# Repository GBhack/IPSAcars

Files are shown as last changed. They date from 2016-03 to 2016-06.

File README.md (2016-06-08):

# IPSAcars : Evolution de véhicules autonomes dans un environnement urbain intelligent

## Description du projet :
Réalisation une maquette simulant un environement urbain comprenant des feux de signalisation "intelligents" (c´est à dire s´adaptant à la circulation) à l´ aide d´ une carte FPGA et, dans le même temps, des véhicules autonomes (à l´ aide d'un BeagleBone) capables de circuler dans cet environnement.

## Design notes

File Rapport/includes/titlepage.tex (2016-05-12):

\begin{titlepage}
\newgeometry{top=2cm,bottom=2cm}

\newcommand{\HRule}{\rule{\linewidth}{0.5mm}} % Defines a new command for the horizontal lines, change thickness here

\center % Center everything on the page
 
%----------------------------------------------------------------------------------------
%   HEADING SECTIONS
%----------------------------------------------------------------------------------------

\\[1.5cm]

\textsc{\Large Projet Electif}\\[0.5cm] % Major heading such as course name
\textsc{\large Projet technique}\\[0.5cm] % Minor heading such as course title

{\normalsize \today}\\[1.5cm]

%----------------------------------------------------------------------------------------
%   TITLE SECTION
%----------------------------------------------------------------------------------------

\HRule \\[0.4cm]
{ \Large \bfseries Evolution de véhicules autonomes dans un environnement urbain intelligent}\\[0.4cm] % Title of your document
\HRule \\[2.5cm]

%----------------------------------------------------------------------------------------
%   LOGO SECTION
%----------------------------------------------------------------------------------------

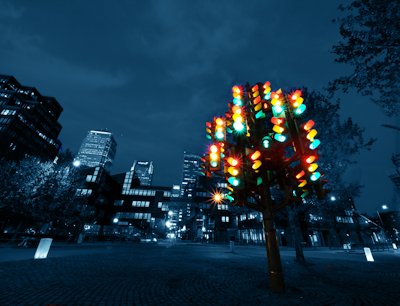
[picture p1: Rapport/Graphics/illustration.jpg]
 \\[2.5cm]

%----------------------------------------------------------------------------------------
%   AUTHOR SECTION
%----------------------------------------------------------------------------------------
{\normalsize Auteurs:}\\
\small
\textsc{Biton} Guillaume (guillaume.biton@ipsa.fr)\\
\textsc{Guichard} Marc-Antoine \small(marc-antoine.guichard@ipsa.fr)\\
\textsc{Lhermite} Camille \small(camille.lhermite@ipsa.fr)\\
\textsc{Monnot} Maxime \small(maxime.monnot@ipsa.fr)\\[1cm]

%----------------------------------------------------------------------------------------

\vfill % Fill the rest of the page with whitespace

\restoregeometry

\end{titlepage}

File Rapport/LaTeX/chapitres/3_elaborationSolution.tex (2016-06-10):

\subsection{Circuit}

	\subsubsection{Structure}

		Le circuit sera principalement composé de medium de 5mm d'épaisseur (matériau résistant, léger, peu fragile, facilement usinable et peu cher) reposant sur une structure une taseaux (de manière à surelever le plateau, afin de passer les câbles en dessous et laisser de la place pour les systèmes de fixation, par exemple ainsi que pour rigidifier la structure (le medium étant un matériau souple)).\\

		Nous avons décidé de donner à la "piste" du circuit la forme suivante :

		\illu{formePiste.pdf}{Forme de la "piste"  du circuit}{0.6}

		Ainsi, nous avons un carrefour à feux ainsi que quatre intersections, soit un large éventail de possibilités.\\

		Après avoir fait une rapide estimation des dimensions de notre robot, nous avons déduit que le circuit devrait faire environ deux mètres par deux mètres.
		Nous avons préféré ajouter vingt centimètres de côté par sécurité.\\

		Ces dimensions étant importantes, ceci nous a conforté dans l'idée que notre circuit devrait être fait en deux parties afin d'en faciliter le rangement. Nous fabriquerions donc deux cadres de deux mètres vingt par un mètre dix qui pourront être facilement assemblés.

	\subsubsection{Feux}

		Les feux seront comprendront chacun deux LED "haute luminosité" de 5mm : une rouge et une verte. Trois fils seront donc nécéssaires pour chaque feu : deux pour les alimentations de chacune des LEDs et une masse commune. Avec les quatre feux, le circuit comptera donc huit LEDs et douze fils différents.\\
		\newpage
		Les feux seront dans la mesure du possible imprimés en 3D :\\
		\begin{figure}[ht!]
			\centering
			\begin{minipage}{0.4\textwidth}
				\raggedleft
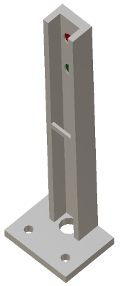
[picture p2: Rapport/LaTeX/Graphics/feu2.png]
				
			\end{minipage}\hfill
			\begin{minipage}{0.4\textwidth}
				\raggedright
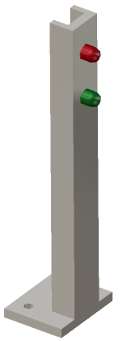
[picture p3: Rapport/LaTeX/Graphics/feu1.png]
				
			\end{minipage}
			\caption{Maquette numérique d'un feu bicolore}
		\end{figure}

		\vspace{15pt}

		Notons la présence de deux petits trous pour enficher les feux sur des vis et d'un plus gros pour le passage des fils. Un passe-câble est également intégré à la "goulotte" qui constitue le montant du feu afin de guider les fils.

	\subsubsection{Capteurs}

		Afin d'adapter le comportement des feux à l'état du trafic, encore faut-il que la carte FPGA dispose d'un moyen d'évaluer ce trafic.\\

		Nous disposerons donc sur la piste des capteurs "ILS" (Interrupteur à Lame Souple) \nomenclature{ILS}{Interrupteur à Lame Souple} sur la piste aux abords des feux. Les ILS sont de petits composants se comportant comme un interrupteur ouvert en temps normal, et comme un interrupteur fermé lorsqu'on approche un aimant.\\

		En munissant nos robots d'un aimant bien placé, ces derniers fermeront temporairement le circuit lors de leur arrivée aux abords des feux.\\

		Cette solution est extremement simple et ne nécéssite aucun traitement du signal (contrairement aux capteurs à effet hall ou fourches optiques, souvent utilisés en détection de présence).

\newpage
\subsection{Robot}

	\subsubsection{Suivi de trajectoire}

		Afin d’offrir une capacité de suivi de trajectoire simple et robuste, il a été décidé d’intégrer au robot la fonctionnalité "suivi de ligne". Il s’agit de l’une des méthodes les plus répandues\cite{bib3} \cite{bib4}, relativement simple à implémenter et économe aussi bien en composants qu’en puissance de calcul nécessaire.\\

		L’idée est d’offrir une base fiable et simple pour que le suivi de trajectoire ne soit pas une source de préoccupation ou d’erreur dans le cas d'utilisations centrées sur d’autres problématiques (dans le cadre d'un TP sur la reconnaissance d'image, par exemple). Cela n’exclut cependant pas qu’un étudiant ou chercheur désireux d’explorer d’autres possibilités de suivi de trajectoire (via la caméra, un dispositif de triangulation ou autre) puisse se passer de ce module et exploiter une autre solution.\\

		Le principe de suivi de ligne est relativement simple : on place sur l’axe du robot, quelques millimètres au-dessus du sol, un capteur appelé « réflecteur optique ». Ce capteur émet une onde lumineuse (souvent infrarouge) et une cellule mesure l’intensité reçue sur la longueur d’onde émise. Une forte intensité reçue indiquera la présence d’une surface réfléchissante, tandis qu’une faible intensité indiquera la présence d’une surface absorbante. Il est ainsi aisé de différencier un fond sombre (la « route ») d’une ligne blanche.\\

		Une loi linéaire lie la tension lue en sortie de capteur à l'intensité reçue.\\
		Une simple lecture de cette tension permet, après comparaison avec des valeurs "seuil" définies expérimentalement, de savoir si le capteur se trouve au dessus d'une ligne blanche ou non.\\

		Sur les schémas suivants, pour des raisons d'imprimabilité et de lisibilité, les lignes seront noires et le revêtement du circuit sera blanc.\\

		\begin{figure}[H]
			\centering
			\begin{minipage}{0.48\textwidth}
				\centering
				
				\caption{Capteur au dessus d'un support sombre}
			\end{minipage}\hfill
			\begin{minipage}{0.48\textwidth}
				\centering
				
				\caption{Capteur au dessus d'un support clair}
			\end{minipage}
		\end{figure}

		La question qui se pose est celle du nombre de capteurs, et de leur disposition.\\

		Il est tout à fait possible de n'utiliser qu'un capteur : chaque fois qu'il quitte la ligne blanche, on entamera un virage à droite (puis à gauche si on ne retrouve pas la ligne blanche dans les quelques millisecondes suivantes) jusqu'à retrouver la ligne. Il est évident que cette méthode ne permettra pas une très grande fluidité de déplacement pour notre robot.

		\illu{capteurSimpleGauche.pdf}{Dépassement de la ligne sur la gauche}{1}
		\illu{capteurSimpleDroite.pdf}{Dépassement de la ligne sur la droite}{1}

		L'utilisation de deux capteurs permet une meilleure fluidité. On placera cette fois un capteur de chaque côté de la ligne.

		\illu{capteurDoubleGauche.pdf}{Dépassement de la ligne sur la gauche}{1.4}
		\illu{capteurDoubleDroit.pdf}{Dépassement de la ligne sur la droite}{1.4}

		Notons que, quelque soit la méthode employée, le suivi de ligne se résume toujours à un "rebondissement" des capteurs sur la ligne. Aussi, pour obtenir une trajectoire aussi rectiligne que possible, il faudra "resserer" les capteurs au maximum autour de la ligne, et appliquer des corrections de faible amplitude.

		\illu{capteurDoubleEcartFort.pdf}{Ecart important entre les capteurs}{1}
		\illu{capteurDoubleEcartFaible.pdf}{Ecart réduit entre les capteurs}{1}

		Nous pourrons éventuellement introduire un amortissement progressif de la correction via un régulateur PID\nomenclature{PID}{Proportionnel, Intégrateur, Dérivateur}, mais cela peut introduire de nombreuses problématiques dans des cas d'utilisation plus complexes.\\

		Nous retiendrons donc à ce stade la solution consistant en deux capteurs placés de part et d'autre de la ligne. Nous veillerons à ce que le placement des capteurs permette une détection de très faibles écarts de trajectoire, sans pour autant induire des ambiguïtés de mesure.\\

		Intéressons nous maintenant au cas d'une trajectoire courbe. Le fait d'avoir privilégié l'application de faibles corrections peut alors s'avérer problématique si ces dernières ne sont pas suffisantes pour adapter la trajectoire.

		\illu{perteTrajectoireVirage.pdf}{Perte de trajectoire en virage dû à de trop faibles corrections}{1.5}

		Pour obtenir un fluidité de déplacement raisonnable tout en assurant la possibilité de suivre des trajectoires courbes à rayon de virage réaliste, nous placerons une deuxième série de capteurs "encadrant" les capteurs principaux. Une détection de ligne par ces capteurs déclanchera une correction plus importante.

		\illu{trajectoireVirage.pdf}{Maîtrise de la trajectoire en virage grâce à l'utilisation de 4 capteurs}{1.5}

		Cette solution consistant en l'utilisation de quatre réflecteurs optiques alignés de manière à encadrer de près la ligne à suivre est sans doute l'une des plus simples imaginables en terme de réalisation mais également d'utilisation et de maintenance.
		Elle n'est malheureusement pas suffisante pour répondre à notre besoin. En effet, cette solution trouvera ses limites dès lors que notre Robot rencontrera sa première intersection, élément capital de ce projet.\\

		\illu{intersection4Capteurs.pdf}{Robot incapable de répondre à la présence d'une intersection}{1.5}

		Si on trouve dans la littérature de très nombreux exemples de réalisations de robots suiveurs de lignes, ces dernières se limitent toujours à des circuits sous forme de boucle. Notre défi est donc de mettre au point une solution permettant l'évolution du robot sur un circuit comprenant des intersections. Notre robot devra ne pas être "perturbé" au passage d'une intersection, mais surtout être capable d'emprunter toutes les directions qui lui sont offertes.\\

		La solution que nous avons mis au point consiste en l'introduction d'un capteur central et l'adoption d'un comportement "mono-latéralement centré" du robot lors de la traversée d'intersections : lorsqu'il arrivera sur une intersection, le robot ne se souciera plus que de garder son capteur central sur la ligne, et ses capteurs latéraux \textbf{du côté de la direction choisie} à l'écart de cette dernière.

		\illu{intersection5CapteursTD.pdf}{Suivi de trajectoire sur une intersection (en choisissant d'aller tout droit)}{1.5}
		\illu{intersection5CapteursDroite.pdf}{Suivi de trajectoire sur une intersection (en choisissant d'aller à droite)}{1.5}

		Notons que la forme de la ligne devra être intelligemment faite, en présentant des rayons de courbure réalistes (un véhicule ne peut pas tourner à angle droit) et des intersections réalisables (notamment via l'utilisation de deux lignes séparées pour la circulation en sens contraires).\\

		Voici donc à quoi ressemblerait un carrefour:
		\illu{carrefour.pdf}{Carrefour en représentation "lignes"}{1.4}

		Pour pleinement définir la logique mise au point, illustrons la au travers de la situation la plus complexe que pourra rencontrer notre robot, qui est celle de la bifurcation à gauche.

		\illu{carrefour5capteursGauche.pdf}{Cas du virage à gauche sur un carrefour avec cinq capteurs}{1.5}

		\begin{enumerate}
			\item Le premier croisement ne nous intéresse pas. Nous allons continuer tout droit et éteignons donc la moitié droite de nos capteurs.
			\item Au passage du croisement, nous éteignons temporairement l'ensemble de nos capteurs.
			\item Le croisement passé, nous éteignons cette fois la moitié gauche de nos capteurs pour ne pas être perturbés par "la voie d'insertion".
			\item Peu de temps après, nous rallumons la moitié gauche et éteignons la moitié droite des capteurs pour suivre la voie bifurquant à gauche.
		\end{enumerate}

		Cette solution semble robuste tout en conservant une certaine simplicité d’implémentation. Elle sous-entend en revanche que le robot "sache" quand il arrive sur une intersection, mais également qu'il puisse évaluer à quelques millimètres près la distance qui le sépare des différentes "parties" de cette intersection (pour activer et désactiver ses capteurs en conséquence).\\

		La solution à cette problématique nous a été inspirée par le souvenir d'un brevet déposé en 2003 par le groupe PSA \cite{bib5}, qui proposait l'utilisation de code-barres tracés sur la route et que des capteurs placés sous le pare-choc des voitures pourraient "lire" pour prévenir le conducteur des sources de danger à venir (intersections, feux...).
		Il fut donc décidé que deux capteurs supplémentaires seraient ajoutés sur les extérieurs. Ils augmenteraient ainsi la précision de placement sur la ligne, mais permettraient surtout de lire des "codes-barres" placés sur la piste. Ces code-barres devraient permettre au robot d'être averti de l'approche d'un carrefour (trois choix de direction possibles) ou d'une simple intersection (deux choix possibles). Nous avons simplement basé notre code sur une ligne simple ou doublée :\\
		\begin{figure}[H]
			\begin{tabu}to \textwidth {@{} | l | *3{X[c]|}@{}}
			  \hline
			   & \textbf{Gauche} & \textbf{Droite} & \textbf{Gauche ET Droite} \\
			  \hline
			  \textbf{Simple} & Impossible de tourner à droite & Impossible de tourner à gauche & Toutes possibilités offertes\\
			  \hline
			  \textbf{Double} & Obligation de tourner à gauche & Obligation de tourner à droite & Impossible d'aller tout droit \\
			  \hline
			\end{tabu}
			\caption{Formalisme employé pour les code-barres}
		\end{figure}

		Un code "doublé" serait composé de deux lignes elles mêmes séparées d'une épaisseur de ligne.
		Les codes seraient placés à 30cm du premier croisement.\\

		Dès la lecture d'un code au sol, le robot sera donc "attentif" à l'éventuelle apparition d'un doublon pendant environ deux centimètres. Si rien n'est lu passé cette distance, il en déduira qu'il s'agit d'un code simple. Il prendra alors une décision de direction (et pourra au passage en avertir les autres robots) et commencera un décompte de distance afin de gérer les activations et désactivations de ses capteurs jusqu'au franchissement de l'intersection.\\

		Illustrons ce système avec le cas de la bifurcation à gauche :

		\illu{carrefour7capteursGauche.pdf}{Cas du virage à gauche sur un carrefour avec sept capteurs}{1.5}

		\begin{enumerate}
			\item Lecture d'un code-barre : dans 30cm le robot aura la possibilité de tourner à droite et à gauche.
			\item Aucun doublon détecté dans les quelques centimètres suivants. La possibilité d'aller tout droit nous est donc offerte. Prise de décision quant à la direction (nous choisissons d'aller à gauche) et avertissement des autres robots en conséquence.
			\item Le premier croisement ne nous intéresse pas. Nous allons continuer tout droit et éteignons donc la moitié droite de nos capteurs.
			\item Au passage du croisement, nous éteignons temporairement l'ensemble de nos capteurs.
			\item Le croisement passé, nous éteignons cette fois la moitié gauche de nos capteurs pour ne pas être perturbés par "la voie d'insertion".
			\item Peu de temps après, nous rallumons la moitié gauche et éteignons la moitié droite des capteurs pour suivre la voie bifurquant à gauche.
		\end{enumerate}

		Le robot doit donc être conscient des distances parcourues avec une précision supérieure à deux centimètres. Le moyen le plus simple d'implémenter cette fonctionnalité est sans aucun doute au travers d'un encodeur incrémental placé sur l'axe de propulsion du robot.\\

		Nous pouvons donc considérer qu'à ce stade, nous disposons d'un solution satisfaisante répondant à la problématique du suivi de trajectoire.
		Cette solution répond précisément aux contraintes du projet, tout en conservant un certain niveau de simplicité. Elle est, pour rappel, constituée des éléments suivants :\\

		\begin{itemize}
			\item \textbf{Sur le circuit :} Un réseau de lignes blanches sur fond noir représentant les trajectoires empruntables par le robot.
			\item \textbf{Sur le robot :} Un ensemble de 7 réflecteurs optiques.
		\end{itemize}

	\subsubsection{Détection d'obstacles et de de signalisation}

		Etant donné le fait que les robots évoluerons dans un environnement idéal, parfait, il n'existera pas en première instance d'obstacles à proprement parler, tel qu'une route barrée aléatoirement, par exemple. Le seul obstacle que nous risquerions de rencontrer est un autre robot situé juste devant nous et arrété à un feu. Ici, le sonar situé à l'avant aura une priorité plus élevée que les autres capteurs, et pourra passer outre les différentes informations reçus par les autres capteurs, influençant fortement la décision. En langage informatique, on parlera d' "override", qui peut être nécessaire dans une situation d'urgence comme celle ci. Ainsi, quelque soit les informations des autres capteurs, le robot s'arretera.
		\\
		Ce point est bien entendu sujet à améliorations, et tout développeur pourra, s'il le désire, implémenter la gestion de ce genre de situations : route barrée, ligne centrale partiellement effacée et peu détectable, etc...
		\\\\
		Dans le cadre de ce projet, cette détection de signalisation se limite aux feux et aux intentions des vehicules comme nous allons le developper en \ref{feuEtIntentions}, page \pageref{feuEtIntentions}. Cependant, il pourra être envisageable à l'avenir de rajouter une signalisation par panneaux (Céder le passage, Stop...).
		Cette partie sera réalisée en utilisant des techniques de reconnaissance d'image en quasi-temps réel, utilisant la caméra embarquée, et initialement développé en Python.
		\\\\
		Notons également qu'une série des tests simples et logiques seront réalisés en cascade. Une fois tous ces tests (détaillés ci-dessous) effectués, le module de décision du robot réalisera une synthèse de tous les résultats, et effectuera un choix.
		\begin{enumerate}
			\item Attente de lecture du premier code-barre
			\item Lecture du premier code-barre
			\item Démarrage du décompte de la distance
			\item Attente de lecture du deuxième code-barre
			\item S'il existe, lecture
			\item Décision sur la direction à prendre
			\item Signalisation des intentions
			\item Recherche du feu de signalisation
			\begin{enumerate}
				\item S'il existe, détermination de sa couleur
				\begin{itemize}
					\item Arrêt à 10 cm s'il est rouge
					\item S'il est vert, on continue
				\end{itemize}
				\item S'il n'existe pas, on se situe à une intersection "classique", recherche d'un robot éventuel
				\begin{itemize}
					\item S'il y a un robot, sommes-nous prioritaire ? Est-il déjà engagé ? On utilisera, en plus de la reconnaissance d'image, le sonar.
					\item S'il n'y en a pas, on continue sans s'inquiéter.
				\end{itemize}
			\end{enumerate}
			\item Une fois que le carrefour ou l'intersection est passé, on éteint toute indication sur nos intentions.
		\end{enumerate}
		Une fois cette séquence terminée, on recommence.
		\\
		En parallèle, une instance vérifiera en boucle si un obstacle se situe devant nous. Si oui, le système d' "override" s'applique. Nous nous arretons et mettons en pause la tâche en cours jusqu'à ce que l'avancée soit possible, plus un délai de sécurité. Le robot pourra se remettre en mouvement et reprendre la tâche mise en pause.

	\subsubsection{Implémentation matérielle}

		\paragraph{Propulsion et direction}

			D’expérience, nous avons constaté que quatre roues complexifient et sur-contraignent les manœuvres directionnelles des robots. Nous avons donc décidé d'adopter la solution la plus répandue en "petite robotique" et consistant en l'utilisation de deux moteurs à courant continu pilotés indépendamment assurant à la fois la propulsion et la direction : on réduira les gaz à droite pour tourner de ce côté et réciproquement. Ces moteurs sont généralement pilotés en "PWM" \nomenclature{PWM}{Pulse-Width Modulation, ou Modulation de Largeur d'Impulsions}, mais d'autres solutions sont possibles et dépendront de notre contrôleur. Beaucoup d'applications utilisent des chenilles ou des courroies en caoutchouc pour assurer la propulsion, mais nous privilégierons l’utilisation de roues à pneus, par soucis de simplification de la conception (l'emploi de chenilles ou de courroies induit  une grande précision d'usinage et de montage pour assurer le parallélisme des poulies et la tension de la courroie) et de réduction des coûts.\\

			L'utilisation d'un seul moteur de propulsion et d'une roue directionnelle pilotée par un servomoteur a longtemps été considérée, mais cette solution s'est révélée bien plus complexe à mettre en place et sans réel intérêt particulier.\\

			\illu{virageDeuxMoteurs.pdf}{Virage à l'aide de deux moteurs indépendants}{1.5}

			L'espacement entre les deux roues $E$ est constant et connu.
			On fixera la vitesse appliquée à la roue à l'extérieur du virage $\omega_{ext}$ comme référence.
			On adaptera donc la vitesse de la roue à l'intérieur du virage $\omega_{int}$ en fonction du rayon de virage $R$ désiré.
			Il s'agit là d'une simple relation de Thales et on définit ainsi :
			\[\omega_{int} = \omega_{ext}\frac{R-E}{R}\]

			On peut donc obtenir n'importe quel rayon de virage en diminuant simplement la vitesse de la roue à l'intérieur du virage.
			L'approximation selon laquelle la tension appliquée à un moteur et sa vitesse de rotation sont linéairement liés sera amplement suffisante dans le cadre de ce projet.\\

		\paragraph{Controleur}\label{Solution-controleur}

			Nous cherchons un contrôleur capable d'embarquer des applications en C (ou ses dérivés) et si possible en Python et/ou Matlab.
			Ce contrôleur devra être capable d'acquérir les données de différents capteurs et de commander deux moteurs au minimum (sans compter d'éventuelles sorties type LEDs).
			Le contrôleur devra également bénéficier d'une puissance de calcul suffisante pour les opérations de reconnaissance d'image.\\

			Ce dernier critère élimine d'office les microcontrôleurs 8 et 16 bits et donc les cartes de type "Arduino" dont la puissance de calcul et la capacité de traitement de flux est bien trop faible pour permettre une reconnaissance d'image supérieure à quelques pixels carrés.\\

			Nous nous sommes naturellement tournés vers la famille des micro-ordinateurs mono cartes. Cette récente catégorie d'ordinateurs propose sur une carte de quelques centimètres de côté et pour moins d'une centaine d'euros un véritable ordinateur avec une connectivité réseau et USB, bien souvent vidéo, une puissance de calcul extrêmement confortable et la capacité de faire tourner des systèmes Linux et dérivés (et donc d’exécuter tous types de codes). Démocratisés en 2011 avec le Raspberry-Pi, ces ordinateurs se sont multipliés et l'offre est aujourd'hui très large. Nous avons ciblé notre sélection sur les plus rependus (qui sont, de par leur succès, bien plus abordables et faciles à se procurer, et bénéficient d'une plus large et solide base documentaire) : les Raspberry-Pis, Beaglebones et UDOOs (pour ne citer qu'eux).\\

			Les UDOOs furent vite écartés en raison de leur prix.
			Le Raspberry-Pi 2 et BeagleBone Green se situent dans la même gamme de prix (autour de 40\$). Nous avons arrêté notre choix sur le BeagleBone Green (BBG\nomenclature{BBG}{BeagleBone Green}): ce dernier, contrairement au Raspberry-Pi 2, ne dispose pas de sortie vidéo (dont nous n'avons pas utilité au sein de ce projet) et possède une puissance de calcul légèrement inférieur à ce dernier (tout en restant parfaitement respectable) mais possède une mémoire intégrée (ce qui dispense de l'achat d'une carte séparée) et surtout de capacités d'entrées/sorties numériques et analogiques bien supérieures. Ce point nous est extrêmement important: en effet, le Raspberry-Pi n'est capable de générer qu'un signal PWM et ne possède aucune entrée analogique ce qui aurait nécessité l'utilisation de "périphériques" supplémentaires pour la gestion des moteurs et des capteur et donc alourdi les coûts et la complexité de conception, augmenté le nombre de sources potentielles de pannes...\\

			Nous utiliserons donc un BeagleBone-Green Wireless :
			\illu{BBG.jpg}{Le BeagleBone Green \textit{\textbf{(source : seeedstudio.com)}}}{0.45}

			Ce dernier est équipé d'un processeur ARM 32bits à 1Ghz, de 512Mo de RAM de 4Go de mémoire embarquée et d'un impressionnante capacité de communication : 7 entrées analogiques (la carte comprend un convertisseur analogique-numérique 12bits), 65 entrées/sorties numériques (0 ou 3.3V) et bénéficie même de fonctionnalités telles qu'un compteur d'impulsion intégré au processeur (particulièrement utile pour l'interfaçage de notre encodeur). La connectivité wifi et bluetooth offre de belles possibilités quant aux interfaces utilisateur et la capacité de communiquer entre robots. La carte consomme moins de 1,5W et coûte 45\$ \cite{bib6}.
			Nous la "chapeauterons" d'une carte d'extension que nous réaliserons nous même pour faire l'interface entre les ports d'extension et nos différents capteurs et actionneurs (voir \ref{carteMere}, page \pageref{carteMere}).\\

			Notons que le BBG doit être alimenté en 5V, et travaille avec un niveau logique "CMOS" de 3.3V. Les entrées et sorties numériques devront donc être compatibles (niveau haut supérieur à 2.5V et inférieur ou égal à 3.3V et niveau bas inférieur à 1.3V).

		\paragraph{Suivi de ligne}\label{solutionSuiviLigne}

			Comme dit précédemment, nous utiliserons sept réflecteurs optiques infrarouges pour effectuer le suivi de ligne.
			Un réflecteur optique est composé d'une LED \nomenclature{LED}{Light-Emitting Diode, ou Diode Electro-Luminescente} (ici infrarouge) et d'un phototransistor. Le phototransistor est comparable à un transistor classique, dont le courant de base serait remplacé par une intensité lumineuse, ou plus simplement encore comme une résistance variable en fonction de l'intensité lumineuse reçue.\\

			Nous utiliserons des TCRT5000, très répandus.\\

			Les capteurs nous fournissent donc une tension variable qu'il faudra pouvoir exploiter : en dessous d'une certaine valeur de cette tension, nous pourrons conclure en la présence d'une ligne blanche (forte réflectivité).\\

			Deux solution s'offrent à nous : ou bien concevoir un montage basé sur un comparateur et une résistance variable (pour régler la valeur seuil) afin d'obtenir une sortie booléenne (par exemple : 5V en présence d'une ligne blanche et 0V sinon) qui pourra très simplement être lue sur n'importe quelle entrée numérique du contrôleur, ou bien tirer partie de l'encodeur analogique-numérique intégré au contrôleur pour lire la valeur directement. Nous privilégierons cette méthode qui permet de limiter le nombre de composants, et donc le coût et les sources de pannes.\\

			Le BeagleBone Green possède sept entrées analogiques (nous avons justement sept capteurs) capables de discerner $2^{12} = 4096$ niveaux différents linéairement répartis entre 0 et 1,8V\cite{bib6}.
			Ainsi, l'application d'une tension de 0V à l'une de ce entrées nous permettra de lire la valeur "0" logiciellement, 2048 pour 0,9V, 4096 pour 1,8V etc... Nous prendrons garde à ne jamais dépasser cette valeur sous peine d’endommager le controleur. Le BBG fournit une tension de 1.8V spécifiquement pour cette application\cite{bib6}.\\

			L'intégration des capteurs est discutée en \ref{integrationReflecteurs} (page \pageref{integrationReflecteurs}).

		\paragraph{Acquisition d'images}

			L'acquisition d'images, pour des raisons évidentes de coûts et  de simplicité d'utilisation, sera réalisée à l'aide d'une webcam standard de bureau, connectée en USB au BeagleBone. Nous avons donc choisi d'utiliser la Webcam Logitech C170 :
			\illu{Logitechc170.png}{Webcam Logitech C170 \textbf{\textit{(source : Logitech)}}}{0.35}
			Compte tenu du fait que les caractéristiques techniques du BeagleBone ne nous permettait pas de traiter de la Haute Définition en quasi-temps réel, et que nous n'avions pas besoin d'un tel niveau de précision, nous nous sommes donc intéressés à cette caméra qui, en plus d'être d'une qualité acceptable, possède un clip de fixation universel, facilitant ainsi la mise en place sur le robot. \\

			L'acquisition logicielle sera réalisée par un script réalisé en \href{https://www.python.org/}{Python}. Avec l'aide du package \href{https://www.http://opencv.org/}{OpenCV}, il est aisé d'interfacer la caméra ainsi que de paramétrer le flux vidéo (taille de l'image, nombre d'images par seconde...) afin d'alléger la charge de traitement de l'image pour ne pas déteriorer les performances du BBG. Les images ainsi récupérées (~10/s) seront ensuite analysées selon plusieurs critères (couleurs et leur position, contours...) afin de participer à une prise de décision fiable et pertinente.
			
		\paragraph{Évaluation des distances}

			\subparagraph*{Distances parcourues}

				L'évaluation des distances parcourues se fera simplement au travers d'un encodeur incrémental placé sur l'un des deux axes de propulsion du robot. Un encodeur incrémental produit au moyen de capteurs optiques ou magnétiques un signal carré dont chaque période correspond au passage d'un élément de référence devant son capteur.
				Ainsi, si on place une roue comprenant quatre éléments de référence (4 aimants, ou 4 obturateurs) régulièrement espacés sur l'axe d'un moteur et le capteur judicieusement, nous pourrons observer un front montant chaque fois que le moteur effectue un quart de tour. En comptant à la fois les fronts montants et descendants, nous connaîtrons les variations angulaires du moteur avec une précision d'un huitième de tour. Et en plaçant un second capteur en quadrature (en déphasage de 90 degrés), notre précision sera doublée.\\

				Le constructeur de nos motoréducteurs, Pololu, propose dans son catalogue un ensemble compatible avec notre motoréducteur comprenant un encodeur à deux capteurs optiques en quadrature et des roues intégrant une mire optique adaptée.

				\illu{encoder.jpg}{Ensemble motoréducteur, roue et encodeur \textbf{\textit{(source : Pololu)}}}{0.25}

				Cette solution nous garantit une compatibilité directe, et nous évite surtout d'avoir à adapter un encodeur (souvent coûteux) sur l'axe entre la roue et le réducteur. L'utilisation des deux capteurs en double fronts nous offre une résolution de 48 impulsions par tour de roue. La roue ayant un diamètre de 42mm, cela nous donne une précision de lecture de :
				\[\frac{\pi \times 42}{48}=2.75mm\]

				Nous pourrons même nous permettre de n'utiliser qu'un capteur et bénéficier ainsi d'une résolution de 5.5mm, répondant largement à nos critères.\\

				Il s'agira ensuite de compter le nombre de fronts montants et descendants sur le signal généré par le capteur.
				Ceci peut se faire simplement en connectant le capteur à une entrée numérique du contrôleur et en observant les changements d'état de cette entrée, mais cette méthode consomme énormément de ressources pour une tâche aussi simple. Une autre solution, quand le processeur le permet, consiste à demander au processeur de détecter les fronts électroniquement et de déclencher un script (compteur) le cas échéant. Cette solution est évidemment préférable lorsqu'elle est disponible.\\

				Par chance, notre processeur ARM-A8 possède cette fonctionnalité et intègre même un module eQEP\cite{bib12} \label{eQEP}\nomenclature{eQEP}{Enhanced Quadrature Encoder Pulse, ou Pulsation d'Encodeur en Quadrature Améliorée} justement dédié au traitement des signaux d'encodeurs en quadrature et qui fera tout le travail à notre place (pour peu que l'on utilise un noyau Linux compatible avec le driver de ce module).

			\subparagraph*{Distance des obstacles}

				La distance avec les obstacles en avant sera mesurée grâce à un sonar HC-SR04. Ce capteur a l'avantage d'être facilement utilisable et est suffisament précis, compte-tenu de notre besoin. De plus, il est également peu sujet aux interférences.
				\illu{sonar.jpg}{Sonar ultrasons HC-SR04 \textbf{\textit{(source : Instructable)}}}{1}
				Cette fonction sera particulièrement utile afin de s'assurer que le robot ne rentrera pas en collision avec un potentiel robot situé sur sa trajectoire.\\
				
				Le principe de fonctionnement est simple : on mesure le temps $t_{echo} $ séparant une impulsion envoyée ("trigger") et le retour de cette impulsion ("echo"). Un simple calcul nous donne ensuite la distance à l'obstacle : $d_{obstacle} = \frac{t_{echo} \times v_{son}}{2}$, avec $v_{son}$ la vitesse du son égale à $340 m.s^{-1}$, selon les Conditions Normales de Température et de Pression.

		\paragraph{Signalisation de ses intentions}

			Nos robots seraient considérés, en théorie de l'intelligence artificielle, comme des "agents". Ils en possèdent en effet toutes les caractéristiques et notamment celle de l'autonomie. Chaque robot est autonome dans le sens où il prend ses propres décisions sans recevoir de commande extérieure. Il est donc primordial que chaque robot puisse avertir les autres de ses intentions, et lui même décrypter les intentions des autres agents.\\

			Nous pourrions atteindre cet objectif en faisant communiquer les robots via un réseau quelconque, mais cela sous-entendrait que ces derniers ne soient capables d'évoluer qu'au milieu de leurs "congénères", ce qui serait parfaitement irréaliste dans la vraie vie. Nous avons donc décidé d'implémenter de simples clignotants et feux stops à LED, simples à mettre en œuvre et universels.

		\paragraph{Interaction avec l'utilisateur}

			Ayant constaté au cours de travaux pratiques qu'il est souvent peu aisé de gérer le déclenchement des séquences de programmes (obligation de passer par des temporisateurs et de brancher/débrancher l'alimentation de la carte), nous avons décidé d'implanter un simple bouton poussoir (qui pourra servir pour démarrer, mettre en pause ou arrêter un programme, par exemple) ainsi qu'un interrupteur commandant l'alimentation de la carte mère (et donc de l'ensemble du système).

		\paragraph{Batterie}

			Pour rappel, voici la liste des composants qu'il nous faudra alimenter :
			\begin{itemize}
				\item Deux moteurs à courant continu\\
				D'après leur fiche technique\cite{bib8}, ces derniers fonctionnent entre 3 et 9V avec un rendement optimal autour de 6V. Leur consommation "axe bloqué" (en couple maximum) est de 1,6A. Une estimation pessimiste de leur consommation en fonctionnement normal consistant à prendre le quart de ce courant, nous pouvons considérer que chaque moteur consommera en moyenne moins de 400mA.
				\item Un BeagleBone Green\\
				Le BBG doit être alimenté en 5V et a une consommation moyenne de 400mA \cite{bib13}.
				\item Sept capteurs IR\\
				Chaque capteur consommant, en tout, environ 35mA.
				\item Une moyenne (généreuse) de 2 LEDs allumées\\
				Avec une consommation d'environ 20mA par LED.
				\item Divers petits composants\\
				Pour lesquels on fera un devis global pessimiste à 100mA.
			\end{itemize}

			Soit une consommation moyenne extrêmement pessimiste de 1600mA.
			La plus haute tension nécessaire (demandée par les moteurs) est d'environ 6V.\\

			Étant donné qu'il est plus difficile de réduire une tension que de l'augmenter, et un moteur à courant continu étant beaucoup plus souple que le reste des circuits électroniques (le moteur ne souffrira pas de tourner à une tension légèrement inférieure) nous privilégierons l'usage d'une batterie de 6V ou plus et d'une capacité supérieure à 1600mAh.

	\subsubsection{Implémentation logicielle}

		Nous ne rentrerons ici pas dans les détails, d'une part car le but n'est pas de procéder à la partie développement dans ce dossier et d'autre part car la partie logicielle représente la part la plus fluctuante de nos robots, destinés à être reprogrammés tout au long de leur cycle de vie. Cependant, nous allons tenter de détailler rapidement l'approche que nous recommandons au sujet du développement logiciel dans le cadre de ce projet.

		\paragraph{Suivi de ligne}

			Le suivi de ligne, en terme de programmation, est une simple problématique de régulation. Nous recueillerons les données issues des différents capteurs, les traiterons, et produirons une réponse au travers des actionneurs.\\

			La question, au delà de celle des logiques et algorithmes utilisés pour produire cette régulation, ici hors sujet, est celle de l’interaction avec les capteurs et actionneurs.\\

			Nos programmes devront faire l'acquisition des données suivantes :
			\begin{itemize}
				\item Données issues des réflecteurs, sous la forme de la valeur de sept tensions.
				\item Données issues de l'encodeur, sous la forme d'un comptage des pulsations.
			\end{itemize}

			Ils devront communiquer leurs ordres en faisant varier la tension aux bornes des moteurs. Ceci se fera au travers de la création d'un signal "PWM".\\

			Il s'agira donc d'établir le lien entre les interfaces d'entrées/sorties du contrôleur et le code à proprement parler.\\

			Sur le BBG, l'un des moyens les plus simples d'effectuer cela est de passer par la bibliothèque Python crée à cet effet par Justin Cooper \cite{bib14} \cite{bib15}. Cette bibliothèque simplifie grandement ce genre d'opérations, et lire la valeur (numérique ou analogique) d'un port, ou changer cette valeur ne prend que deux lignes de code (se référer à la documentation).\\

			Une utilisation des entrées/sorties reste néanmoins possible et accessible en C et C++, par exemple \cite{bib16}, mais nous favoriserons l'utilisation de Python pour des raisons "d'affinité", mais également car ce langage simplifie l'utilisation de nombreux outils nécessaires à ce projet, notamment la communication réseau et le traitement d'images, et ne nécessite aucune compilation.\\

			Nous veillerons cependant, toujours dans un soucis de modularité, à ce que nos "modules" python, soient compatibles avec d'éventuelles réalisations en C, java ou autre (voir \ref{integrationLogicielle} : Intégration Logicielle, page \pageref{integrationLogicielle}).

		\paragraph{Reconnaissance d'image}\label{feuEtIntentions}

			La reconnaissance d'image sera utilisée à plusieurs fins :
			\begin{itemize}
				\item \textbf{Couleur du feu}
					La détection de la couleur du feu est un aspect primordial de ce projet. Grâce au package OpenCV, il est très facile de décomposer le spectre de la lumière visible, et donc de déterminer s'il y a en face de nous une lumière verte ou rouge, comme le montre la figure suivante :
					\begin{figure}[H]
					    \centering
					    \begin{subfigure}[h]{0.5\textwidth}
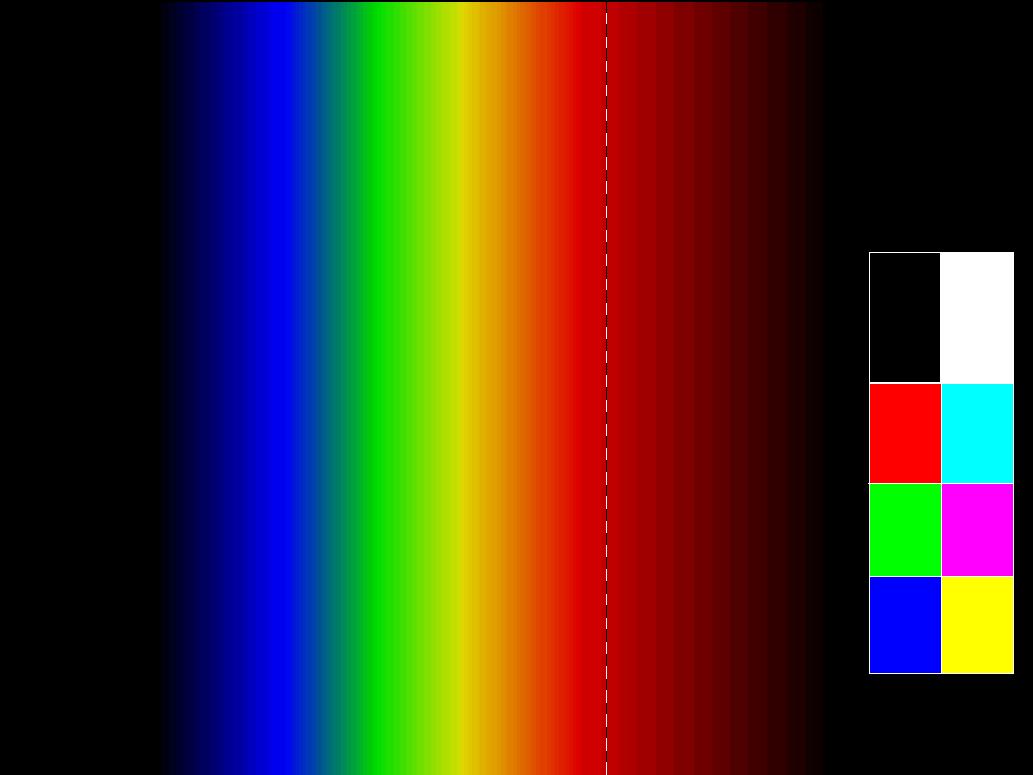
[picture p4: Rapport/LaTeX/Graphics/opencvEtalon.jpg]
					        
					        \caption{Spectre de la lumière visible \textit{\textbf{(source : http://physique-eea.ujf-grenoble.fr/)}}}
					    \end{subfigure}\\

					    \begin{subfigure}[h]{0.3\textwidth}
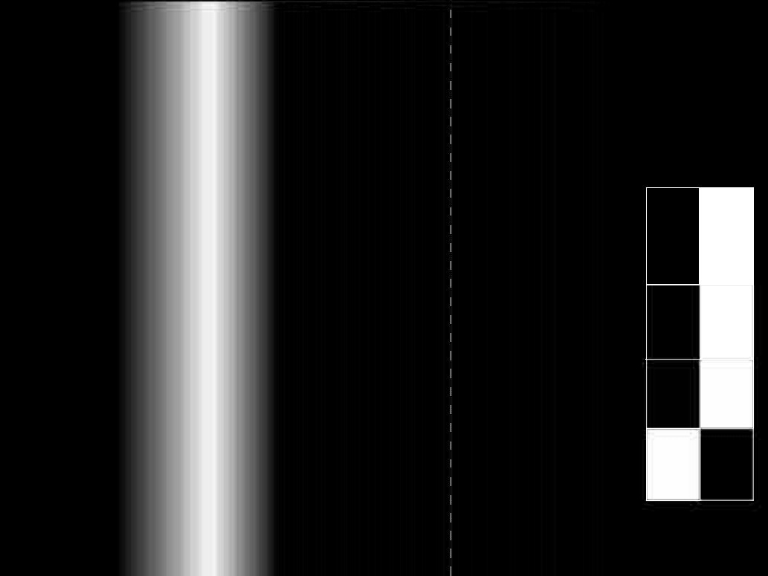
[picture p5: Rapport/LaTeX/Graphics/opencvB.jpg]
					        
					        \caption{Filtre bleu}
					    \end{subfigure}
					    ~ %add desired spacing between images, e. g. ~, \quad, \qquad, \hfill etc. 
					      %(or a blank line to force the subfigure onto a new line)
					    \begin{subfigure}[h]{0.3\textwidth}
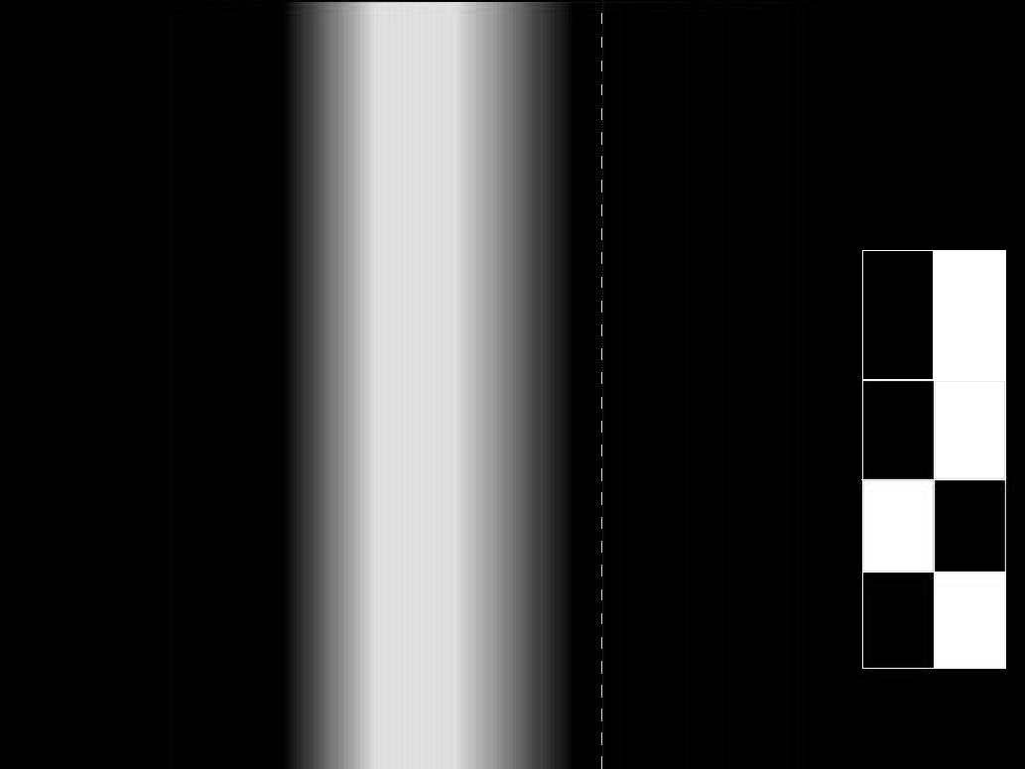
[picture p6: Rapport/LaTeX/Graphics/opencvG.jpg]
					        
					        \caption{Filtre vert}
					    \end{subfigure}
					    ~ %add desired spacing between images, e. g. ~, \quad, \qquad, \hfill etc. 
					    %(or a blank line to force the subfigure onto a new line)
					    \begin{subfigure}[h]{0.3\textwidth}
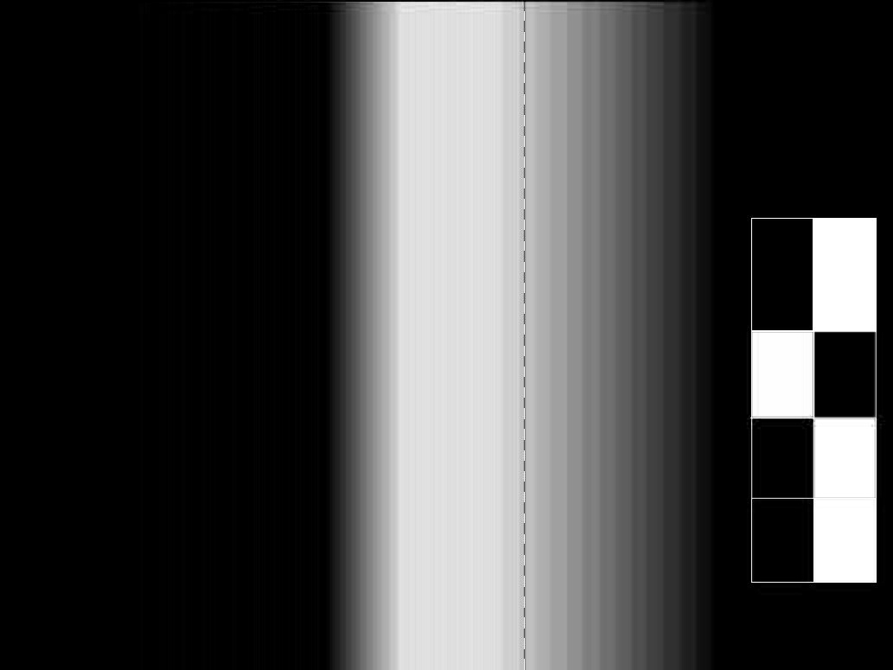
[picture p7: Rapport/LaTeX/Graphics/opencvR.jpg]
					        
					        \caption{Filtre rouge}
					    \end{subfigure}

					    \caption{Spectre (a), selon différents filtres (b),(c) et (d).}
					\end{figure}

					Pour des soucis d'optimisations et de résultats, nous n'utiliserons pas le système Rouge-Vert-Bleu classique, mais plutôt le système HSV\label{HSV}\nomenclature{HSV}{Hue-Saturation-Value, ou Teinte-Saturation-Valeur}, plus adapté à notre problématique :

					\begin{figure}[H]
						\centering
						\begin{subfigure}[h]{0.35\textwidth}
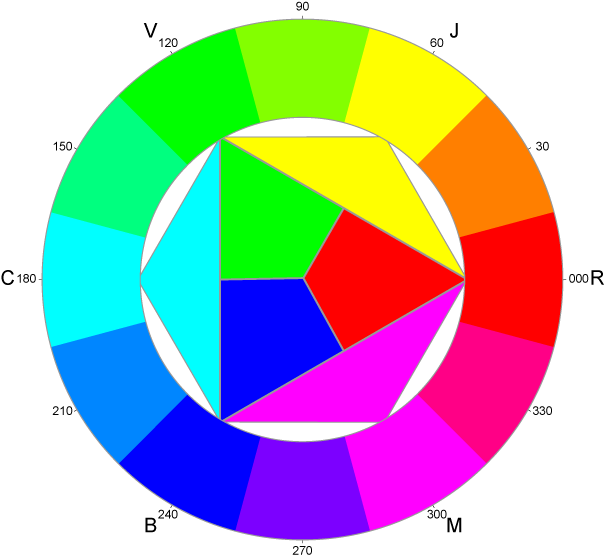
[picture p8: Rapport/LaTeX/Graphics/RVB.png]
					        
					        \caption{Modèle RVB}
					    \end{subfigure}
					    ~
					    \begin{subfigure}[h]{0.35\textwidth}
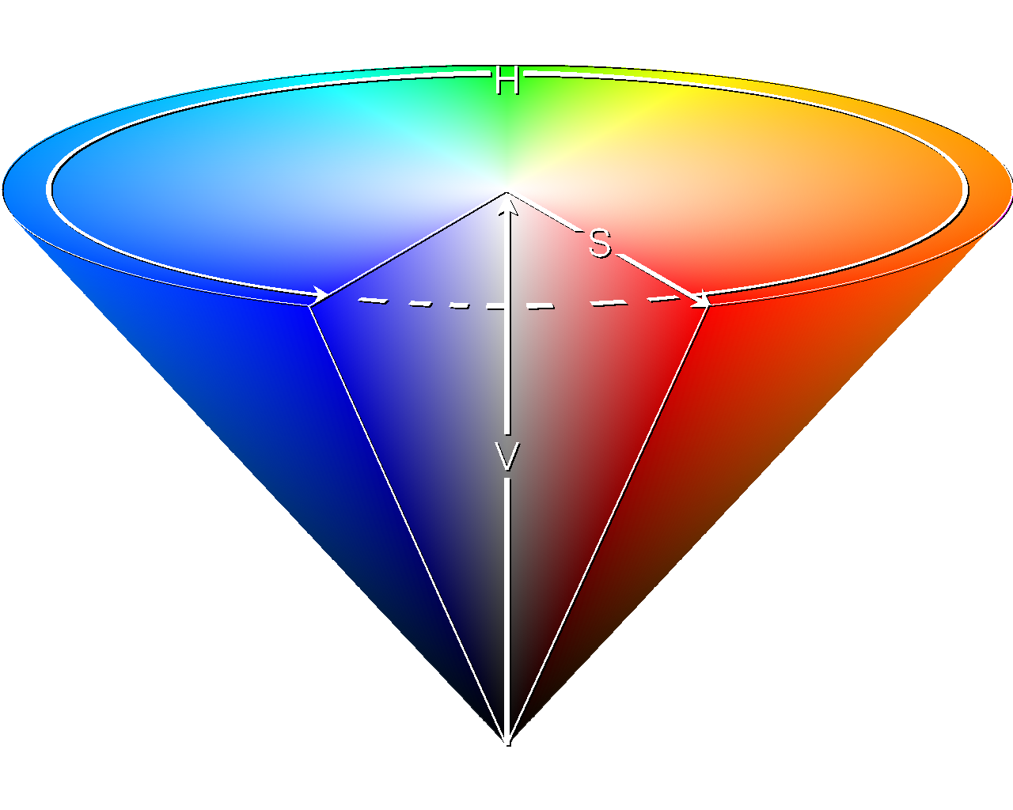
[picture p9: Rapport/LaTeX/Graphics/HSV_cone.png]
					        
					        \caption{Modèle HSV}
					    \end{subfigure}
					    \caption{Comparaison RVB / HSV}
					\end{figure}
					Grâce à ce système, il nous suffit de définir expérimentalement les bornes autour de nos 3 axes de couleurs afin de créer un \textit{masque}. Un masque est ici une image (une matrice, un tableau à deux dimensions); chaque case contenant "1" ou "0". Si "0", le pixel n'a pas passé le filtre : il ne nous intéresse pas. En revanche, si "1", ce pixel et ses environs sont potentiellement interessants et devront être analysés. Nous y reviendrons.\\
					La fonction \textit{inRange} est prévue à cet effet, et nous permet de réaliser un tel masque : 
					Nous déterminerons expérimentalement des bornes pour les variables Teinte ($H_{min}$ et $H_{max}$), Saturation ($S_{min}$ et $S_{max}$) et Valeur ($V_{min}$ et $V_{max}$). Soit un pixel $p$ positionné en $i$ avec pour composantes $H_{i,p}$,$S_{i,p}$,$V_{i,p}$, nous aurons la relation suivante :
					\\ 
					$D_i = H_{min} \leqslant H_{i,p} \leqslant H_{max} 	\land S_{min} \leqslant S_{i,p} \leqslant S_{max} \land V_{min} \leqslant V_{i,p} \leqslant V_{max}$ \cite{bib20}
					\\
					Avec $D_i$ valant VRAI ou FAUX. Si $D_i$ est FAUX, cela signifie qu'il n'y a aucune corrélation entre la couleur détectée et notre objet. En revanche, s'il est VRAI, alors notre objet existe PROBABLEMENT dans notre champs de vision. Nous définirons donc expérimentalement deux couples de triplets (correspondant aux bornes pour le feu vert et le feu rouge). De plus, en utilisant les fonctions d'érosion (\textit{erode}) et de dilatation (\textit{dilate}), nous suprimons les pixels parasites qui passeraient le premier filtre, gardant ainsi uniquement le feu.
					\\

					Une autre problématique est la distance à laquelle le robot doit s'arrêter. En effet, si le feu est rouge, il ne faut pas qu'il s'arrête juste à côté de celui-ci : il risquerait de ne pas le voir passer au vert et de rester bloqué. Compte tenu des vitesses engagées et de l'inertie des moteurs et du robot, nous négligerons la distance de freinage.
					Le schéma suivant résume la situation :
					\illu{distEval.pdf}{Schéma de principe de l'approche d'un feu}{0.35}
					Connaissant l'angle de vue de la caméra (58°)\cite{bib18}, et en utilisant des fonctions géométriques simples, nous pouvons déterminer rapidement la distance minimale au feu s'il faut s'arrêter : $d_{min} = 15 cm \times tan(\frac{58}{2}) = 8,3 cm$. En ajoutant une distance de sécurité puisque la distance de freinage est négligée, nous pouvons ainsi déterminer le moment à partir duquel le robot passera le feu quoi qu'il arrive. Cette distance est établie arbitrairement à 10 cm.\\

				\item \textbf{Présence et intentions des autres utilisateurs}

					Les feux sont les plus simples à gérer. En effet, il ne peut y avoir qu'une et une seule position pour un unique feu. Il suffit "juste" de détecter si oui ou non la couleur dans l'intervalle sélectionné existe. Détecter les intentions d'un autre robot est autrement plus difficile. En effet, compte tenu de la disposition des différents clignotants, nous voyons quoi qu'il arrive 3 des 4 clignotants du robot, s'il ne va pas dans le même sens que nous. \\
					Un bon exemple d'un aperçu de la vue du robot est donné par la figure \ref{robotVueExemple}, page \pageref{robotVueExemple}.
					Après filtrage d'après la méthode indiquée ci-dessus, il faudra récupérer sur le masque de l'image obtenu les différentes tâches en utilisant une méthode \textit{itérative} appelée MeanShift ("Déplacement de moyenne"). Le principe est simple : on choisit un point de coordonnées $(x_0,y_0)$. Autour de ce point, on définit une zone correspondant à la zone d'étude de rayon $r$. On calcule donc la moyenne des coordonnées de chaque "1" du masque contenu dans la zone d'étude. Si aucun n'est contenu dans l'intervalle $[x_0 - r \leqslant x \leqslant x_0 + r ; y_0 - r \leqslant y \leqslant y_0 + r ]$, on décale le point en dehors de ce rayon. Sinon, calcule la moyenne des coordonnées des points compris dans cet intervalle. On obtient ainsi un nouveau point coordonnées $(x_1,y_1)$. L'opération est \textit{réitérée} autant de fois que nécessaire pour déterminer la position d'une LED. Cet algorithme permet de \textit{converger} vers la plus grande densité de points du masque : la LED. Le schéma suivant illustre le fonctionnement de cette méthode.
					\illu{meanShiftMethode.pdf}{Principe de fonctionnement de la méthode "MeanShift" à 3 itérations}{1.2}
					Le même procédé est appliqué une seconde fois. L'algorithme veut qu'un point "cherchant une LED" ne rentre pas dans la zone d'étude d'un autre point ayant déjà localisé une LED, afin de ne pas créer de doublon pouvant fausser les résultats. Si cette deuxième recherche de led est infructeuse, cela signifie que l'on se situe dans un des deux cas suivants :

					\begin{figure}[H]
						\centering
						\begin{subfigure}[h]{0.2\textwidth}
					        
					        \caption{Robot à gauche tournant à gauche}
					    \end{subfigure}
					    ~
						\begin{subfigure}[h]{0.35\textwidth}
					        
					        \caption{Robot devant tournant à droite}
					    \end{subfigure}
					    ~
					    \begin{subfigure}[h]{0.2\textwidth}
					        
					        \caption{Robot à droite tournant à droite}
					    \end{subfigure}
					    \caption{Cas d'une seule LED détectée}
					\end{figure}
					Si une situation comme cela apparait, on repère la position abolue de la LED. Si celle-ci se trouve sur la moitié droite du masque, cela signifie que l'on se situe dans le cas (c). Si la LED se situe sur le bord gauche, deux possibilités s'offrent à nous : soit on se trouve dans la situation (b), auquel cas on se situera au carrefour. Si notre feu est vert et que l'on décide de tourner à gauche également, il faudra combiner ces données au sonar. Si on décide d'aller tout droit ou à droite, on pourra traverser le carrefour sans soucis. En revanche, si on se trouve dans la situation (a), on a à nouveau deux possibilités : soit on se situe au carrefour central auquel cas un des deux robot sera arrété à cause du feu, donc aucun danger, soit on se trouve à une intersection : la règle de la priorité à droite d'applique, nous pouvons avancer sans être inquiétés.
					\\
					Voici les trois autres cas restants :
					\begin{figure}[H]
						\centering
						\begin{subfigure}[h]{0.2\textwidth}
					        
					        \caption{Robot devant tournant à gauche}
					    \end{subfigure}
					    ~
						\begin{subfigure}[h]{0.35\textwidth}
					        
					        \caption{Robot devant tournant à gauche}
					    \end{subfigure}
					    ~
					    \begin{subfigure}[h]{0.2\textwidth}
					        
					        \caption{Robot à droite tournant à gauche}
					    \end{subfigure}
					    \caption{Cas de deux LEDs détectées}
					\end{figure}

					Une fois encore, on réalise un masque et on repère la position des 2 LEDs. Cette fois, on "découpe" le masque en trois verticalement : si les LEDs sont dans le tier de gauche (a), l'agent est à gauche et désire tourner à droite. Si les LEDs sont dans le tier de droite (c), le robot, situé à droite, souhaitera tourner à gauche, et donc croiser notre trajectoire. Il s'agira là de faire respecter la règle de la priorité à droite. Enfin, si celles-ci sont dans le tier du milieu (b), cela signifie que le robot est en face et désire tourner à gauche, et croiser notre trajectoire.
					\\
					On démontre ainsi ici qu'avec une simple asymétrie, on arrive facilement à prédire le comportement des autres usagers.
					\\
					D'un point de vue plus généraliste, si nous considérons une voiture autonome, la détection visuelle des intentions des utilisateurs alentours est une étape à considérer pendant la phase de transition correspondant à l'apparition des voitures autonomes sur le réseau urbain.
			\end{itemize}

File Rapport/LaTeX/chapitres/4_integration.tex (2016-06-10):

\subsection{Circuit}

	\subsubsection{Intégration Matérielle}

		\paragraph{Circuit en lui-même}
			Notre circuit sera donc bien composé de deux parties, chacune constituée d'un panneau de médium monté sur un cadre en tasseaux.
			D'autres problématiques ont fait leur apparition en cours d'étude du projet et c'est ainsi que l'on intègrera des perçages pour la fixation des feux et le passage des fils, mais surtout pour l'intégration des fameux "caches" permettant d'isoler visuellement les "rues".\\

			Les panneaux seront peints en noir et recouverts de scotch d'électricien blanc représentant les lignes. Nous obtenons ainsi un rapport de contraste idéal (noir mat du bois et blanc brillant du ruban adhésif). Le plan à l'échelle de la piste est le suivant :
			\illu{CIRCUIT.pdf}{Plan à l'échelle de la piste}{0.065}

			\vspace{15pt}

			Y apparaissent les lignes, code-barres et caches (en gris plein) évoqués dans le dossier. Les rayons de courbure sont de 75mm, et l'espacement entre les voies et divers obstacles de 220mm.\\

			Un plan contenant toutes les côtes sera produit et pourra être "recopié" à l'aide de simple matériel scolaire (compas, règle, équerre) sur les panneaux avant d'être recouvert par le ruban adhésif.\\

			Les capteurs ILS seront fixés aux panneaux.\\
			On prévoiera des vis "dépassant" aux emplacements appropriés afin de pouvoir y "emboiter" les feux.\\

			Le câblage des capteurs et des feux sera solidaire de chaque partie, et passera par des trous prévus à cet effet dans les tasseaux pour converger en un "faisceau" terminé par un connecteur pour chacune des deux parties. Un connecteur sera présent du côté de chaque feu avec suffisemment de longueur de câble pour pouvoir facilement procéder à l'installation desdits feux.

			Voici à quoi ressemblerait le circuit (les petits éléments ne sont pas visibles):
			\illu{CIRCUIT2.png}{Modélisation 3D du circuit}{0.12}

		\paragraph{Carte électronique}

			La carte aura pour but de servir d’interface entre la carte FPGA et les composants électroniques du circuit (LEDs des feux bicolores et capteurs ILS).\\
			Comme évoqué précédemment, deux faisceaux de câbles terminés par des connecteurs arriveront sur cette carte (un pour chaque moitié de circuit). Ces faisceaux seront constitués de dix fils correspondant à :

			\begin{itemize}
				\item Masse feu 1
				\item Masse feu 2
				\item LED verte feu 1
				\item LED rouge feu 1
				\item LED verte feu 2
				\item LED rouge feu 2
				\item Retour ILS 1
				\item Retour ILS 2
				\item Alimentation ILS 1
				\item Alimentation ILS 2
			\end{itemize}

			Les cartes FPGA Basys 2 utilisées à l’IPSA disposent de quatre ports d’extensions dits « pmod » \cite{bib22}. Ces ports ont un format on ne peut plus standard : connecteurs femelles espacés d’un dizième de pouce (2,54mm).\\
			Chaque connecteur fournit 6 contacts :\\
			\begin{itemize}
				\item Une sortie 3,3V
				\item Une Masse
				\item 4 ports d’entrée/sorties directement mappés sur le FPGA.
			\end{itemize}

			\illu{pmod.png}{Illustration d'un port "pmod" \textbf{\textit{(source : Digilent)}}}{0.4}

			Les LEDs seront commandées par des ports du FPGA configurés en sortie.\\
			Pour ne pas tirer trop de courant sur ces ports (qui ne sont pas fait pour : il sont conçus pour produire des signaux et non des alimentations) et pouvoir fonctionner aussi bien en logique TTL que CMOS, nous passerons par un circuit intégré de la famille 74HC (\textbf{attention à bien différencier la série 74HC de la série 74HCT que nous serons également amenés à utiliser : elles n'ont pas les mêmes tensions de référence !}). 
			Ces portes logiques reposent sur la technologie « collecteur ouvert » et peuvent donc être utilisés comme des transistors de faible puissance. Les entrées logiques correspondent aux bases, les sorties aux émetteurs et l’alimentation du composant (Vcc) aux collecteurs.\\

			La datasheet \cite{bib24} nous apprend qu’ils peuvent fournir jusqu’à 50mA en sortie sur l’ensemble des sorties. En répartissant 4 LEDs par circuit logique et en utilisant ces dernières à 10mA (largement suffisant pour des LEDs  haute luminosité), nous restons en dessous de cette limite même lorsque les 4 LEDs sont allumées simultanément (ce qui en théorie ne devrait pas être le cas).
			Nous utiliserons le 74HC04 qui est un sextuple inverseur (seul 4 éléments seront utilisés). Ainsi, en plaçant un « 1 » (3.3V ou 5V : les deux fonctionnent puisque le composant reconnaît une valeur haute à partir de 2,3V) en entrée, nous obtenons 0V en sortie. En y plaçant un « 0 » (0V), nous obtenons un 3.3V jusqu 20mA par sortie pour un total de 50mA maximum ! Le tout sans jamais prélever plus d’un milliampère en entrée (et donc en sortie du FPGA).\\

			Les sorties du 74HC04 pourront être directement connecés aux anodes des LEDs via une résistance appropriée (150$\Omega$ pour une LED rouge à 1,8V de chute et 100$\Omega$ pour une LED verte à 2,3V de chute).\\

			L’acquisition des états des capteurs ILS est encore plus simple : les ILS étant de simples interrupteurs, on placera l’une de leurs bornes à la masse et on connectera l’autre à une entrée du FPGA en intercalant une résistance de pull-up placée à 3.3V.\\
			Ainsi, la carte FPGA verra un signal stable au niveau haut qui ne passera au niveau bas que lorsqu’un aimant excite le capteur.\\

			Nous pourrions simplifier et « sécuriser » le circuit en intégrant une partie de la logique de fonctionnement de manière électronique (penser le circuit pour que deux LEDs du même feu ne puissent-être allumées simultanément, par exemple), mais ceci irait à l’encontre de la vocation pédagogique du système et limiterait sa capacité d’évolution.\\

			Nous utiliserons de simple connecteurs sécables standard pour connecter le circuit à la carte Basys 2. Ainsi, on pourra directement « enficher » les deux cartes. Mais si l’IPSA venait à acheter de nouvelles cartes FPGA, l’utilisation de simples câbles « strips » permettra de se dispenser de refaire la carte.\\

			\illu{secable.png}{Illustration d'un connecteur sécable 0.1'' standard \textbf{\textit{(source : Gotronic)}}}{0.5}

			Nous aurions voulu mettre en place un système permettant de s’assurer que la carte ne peut être branchée que « dans le bon sens » (avec des connecteurs asymétriques par exemple) mais nous dépendons des connecteurs de la Basys 2 et ne pouvons implémenter cette sécurité. Il faudra donc être extrêmement attentifs à l’utilisation qui sera faite des cartes pour ne craindre aucun dommage (un analyse rapide des schémas nous montre cependant que peu de mal peut être infligé par un mauvais branchement). Surtout, la carte Basys2 est équipée sur ses ports pmod de diodes et résistances de protection \cite{bib23}.

	\subsubsection{Intégration Logicielle}

		Le cas du feu de circulation s'adaptant au trafic est l'exemple type de la logique dite de "l'automate fini". La littérature ne manque pas à ce sujet et nous avons même eu l'occasion de l'étudier au cours de notre cursus.\\

		La logique VHDL \nomenclature{VHDL}{VHSIC1 Hardware Description Language : langage destiné à la programmation de cartes FPGA.} est particulièrement adaptée à ce type de problématique et offre la possibilité de coder un certain nombre d'états et de définir les conditions et modalités de changement d'état.\\

		Dans notre cas, nous compterions trois états:
		\begin{itemize}
			\item \textbf{Etat 0} : Tous les feux au rouge.
			\item \textbf{Etat 1} : Couple de feux A au rouge et couple B au vert.
			\item \textbf{Etat 2} : Couple de feux B au rouge et couple A au vert.
		\end{itemize}

		\vspace {12pt}
		Une succession classique d'états serait 0->1->0->2->0->...\\
		Pour simplifier l'organisation du programme, nous pourrions créer un état intermédiaire entre 1 et 2, identique à l'état 0.\\

		Un diviseur d'horloge permettrait de générer des événements à intervalles réguliers afin de cadencer le changements d'états.\\
		Les capteurs eux-mêmes pourraient générer un événements (sur un front montant de l'entrée logique à laquelle ils sont branchés par exemple) qui, si un certain nombre de conditions sont réunies, anticiperaient le changement d'état (si une voiture se présente à un feu rouge et qu'aucune ne "profite" des feux verts, alors il est plus logique d'inverser cet état).

\subsection{Robot}

	\subsubsection{Intégration Matérielle}

		\paragraph{Ensembles propulsifs}

			Les deux "ensembles de propulsion" seront placés à l'arrière du robot. Une simple bille multidirectionnelle sera placée l'avant pour assurer la stabilité du robot.\\

			Le choix de notre motoréducteur fut basé sur un ensemble de critères :
			\begin{itemize}
				\item Le motoréducteur doit nous permettre d’atteindre une vitesse de pointe minimum de 15 cm/s (environ 70 tours par minute pour une roue de diamètre 4cm).
				\item Le motoréducteur devrait bénéficier d'un couple "confortable" pour les manoeuvres du robot.
				\item Le moteur ne devra pas être surdimensionné de manière à maîtriser la consommation d’énergie.
				\item On se munira du moteur le moins cher répondant aux critères précédents.
				\item Nous désirions aussi dans la mesure du possible trouver un moteur possédant un encodeur intégré, cependant ce critère ne correspond pas à un critère d’arrêt.
			\end{itemize}

			Nous avons estimé le couple minimum nécessaire à 0,01Nm par moteur (en effectuant le calcul pour différentes masses et inclinaisons de la piste).\\

			Il a ensuite fallu composer avec l'offre limitée présente sur le marché "semi-amateurs".\\

			Nous avons finalement sélectionné le motoréducteur "High-Power" de Pololu dans sa version proposant un taux de réduction de 298 pour 1.
			Ce moteur propose les caractéristiques suivantes :\cite{bib8} \\

			\begin{itemize}
				\item Couple de blocage de 0,5Nm
				\item Vitesse à vide sous 6V de 100 tours par minute
				\item Courant à couple maximum de 1.6A (soit 400mA maximum en utilisation normale)
			\end{itemize}

			Ce motoréducteur est associable avec une roue et un encodeur du même constructeur qui forment un ensemble fonctionnel et simple à implémenter. Nous y associerons un support PVC adapté pour la fixation.\\
			Notons qu'un seul des deux moteurs sera équipé d'un encodeur, deux étant superflus et évidemment plus chers.

			Le motoréducteur est équipé de deux fils d'alimentation. Nous les connecterons à la carte-mère au travers d'un bornier. Un double pont en H intégré L293D (comprenant les diodes de roue libre \cite{bib17}) permettra de faire le lien entre le signal PWM généré par le BBG (3.3V limité à une vingtaine de milliampères) et le moteur (que l'on alimentera directement sur la batterie, le signal PWM étant donc adapté sur une base 7.2V). Trois sorties seront donc utilisées sur le BBG pour chacun des deux moteurs : une PWM pour gérer la puissance transmise au moteur, et deux digitales pour le sens de rotation. Ces signaux (de 3.3V) pourront-être directement transmis au double pont en H (le L293D ayant une tension "niveau haut" de 2,3V \cite{bib17}). Nous compterons deux sources d'alimentation pour le pont en H : une alimentation de 5V pour le circuit logique et une alimentation directe sur la batterie (on pensera à intégrer deux condensateurs pour filtrer le bruit dû aux moteurs). Les signaux logiques viendront directement du BBG.\\

			Pour plus de détail, voir \ref{carteMere} (page \pageref{carteMere}).\\

			L'encodeur peut, d'après sa fiche technique \cite{bib9} fonctionner en 3.3V. Cependant, la diode émettrice IR perdra alors de son intensité. Nous procéderons donc à une expérience pour définir si ce fonctionnement en "sous régime" de la diode est satisfaisant. Dans le cas contraire, nous alimenterons l'encodeur en 5V et procéderons à une division de tension sur le signal de sortie avant de le transmettre au BBG, pour ne pas endommager ce dernier. Notons qu'un seul des deux "canaux" de l'encodeur nécessitera d'être connecté au BBG étant donné notre besoin de précision. Ainsi, la carte- mère devra comprendre un connecteur trois contacts dédié à l'encodeur : deux contacts serviront simplement à l'alimentation, et le troisième (le signal) sera connecté à l'une des entrées du BBG permettant l'utilisation du module eQEP (voir \ref{eQEP}).

		\paragraph{Carte Réflecteurs Optiques}\label{integrationReflecteurs}

			Rappelons que nous utiliserons les entrées analogiques du BBG pour effectuer l'acquisition des données du capteur, et que ces dernières sont limitées à 1.8V (voir \ref{solutionSuiviLigne}, page \pageref{solutionSuiviLigne}).

			La datasheet du TCRT5000 \cite{bib7} nous apprend que la LED émettrice possède une tension directe de 1.25V et n'accepte que jusqu'à 60mA.
			Afin de ne pas surcharger la sortie à 1.8V fournie par le BBG (qui ne fournit pas plus de 50mA), nous alimenterons les LEDs en 5V via une résistance de 120$\Omega$, faisant ainsi traverser la LED par $\frac{5-1.25}{120}=31mA$, ce qui est idéal (intensité IR\nomenclature{IR}{Infra-Rouge} suffisamment élevée sans risquer "d'éblouir" les autres capteurs ou de griller la LED).\\

			On connectera le collecteur du phototransistor à la ligne 1.8V au travers d'une résistance de pull-up de 2.7k$\Omega$, la valeur la plus élevée de résistance nous permettant d'assurer un courant de collecteur de 5mA (comme recommandé dans la datasheet). Nous choisissons la valeur la plus élevée afin de limiter la consommation en courant, mais surtout d'augmenter la sensibilité du capteur (il sera ainsi plus facile au phototransistor de "tirer" la tension vers le bas).\\

			Nous avons donc le schéma de principe suivant :
			\illu{reflecteur.pdf}{Schéma de principe d'un réflecteur optique}{2}

			Ce schéma sera reproduit sept fois sur une carte dédiée, qui sera placée à l'avant du robot, parfaitement centrée et placée quelques millimètres au dessus de la piste (la datasheet nous apprend que la distance de fonctionnement idéale entre le capteur et le support est de 2.5 mm, avec un domaine de fonctionnement allant de 0.2 à 12mm).\\
			
			Sachant que la ligne au sol aura une épaisseur de 15mm, nous placerons les trois capteurs centraux de manière à ce que, lorsque le capteur central est placé au milieu de la ligne, il ne manque que 2 à 3mm aux deux autres pour y arriver . Les autres capteurs pourront avoir un écartement légèrement plus élevé :

			\illu{espacementReflecteurs.pdf}{Espacement des réflecteurs optiques}{0.8}

			Notons que la distance exacte entre les capteurs ne pourra être précisément définie que par l'expérience. En effet, nous n'avons aucune indication quant à la largeur du champ de détection du capteur.\\

			Nous connecterons la carte au moyen d'une nappe HE10 à 10 connecteurs.\\

			Le schéma électronique et les gerbers du circuit imprimés sont disponibles en annexe \ref{schemasCarteReflecteurs} (page \pageref{schemasCarteReflecteurs})

		\paragraph{Carte-Mère}\label{carteMere}

			La carte mère est le circuit imprimé permettant de relier véritablement les actions "logicielles" aux actions réelles. Les contraintes pour cette carte sont simples :
			\begin{itemize}
				\item De taille raisonnable, soit de la taille bu BBG
				\item Ne pas intégrer directement les composants ayant un impact sur l'environnement du robot (moteur, LEDs...), pour qu'en cas de défaillance, ainsi que toujours dans un esprit de modularité et d'amélioration continue, un élément soit interchangeable rapidement, par le biais de connecteurs standards.
				\item Facilement intégrable au BBG. L'idée est vraiment de réaliser un shield enfichable simplement.
			\end{itemize}

			Ce shield intègre une prise standard de type Barrel jack, et peut être alimenté par toute source de tension supérieure à 7V. 
			\illu{barrelJack.jpg}{Embase Barrel Jack \textbf{\textit{(source : Conrad.fr)}}}{0.1}
			En effet, les moteurs demandant plus de 5v, il fallait trouver un moyen d'abaisser cette tension. Nous avons donc opté pour un régulateur de tension à découpage, réglé à 5v. Le principe est simple : Un PWM est généré avec comme tension haute la tension d'entrée. En modulant cette impulsion et en faisant passer le signal par un filtre passe-bas, on lisse le signal à une valeur donnée (ici, 5v). L'inconvénient de ce genre de régulateur par rapport aux régulateurs est qu'ils nécessitent plusieurs composants. Mais le principale avantage réside dans leur rendement : jusqu'à 95\% \cite{bib25} ! Un régulateur de tension classique "tranforme la tension d'entrée en excès" en chaleur. Ainsi, pour une entrée à $7,2v$ et une sortie à $5v 1A$, la puissance dissipée est de $P = (V_{in} - V_{out}) \times I = (7,2 - 5) \times 1 = 2,2 W$ ! De plus, sachant que l'intensité en entrée est la même que l'intensité en sortie, on obtient un rendement $R = \frac{V_{out}}{V_{in}} = \frac{5}{7,2} = 69\%$. Une alimentation à découpage, bien qu'un peu plus onéreuse, permettra donc d'augmenter considérablement l'autonomie.\\
			La carte BBG n'étant pas capable de fournir une intensité maximum élevée, nous avons décidé d'utilisé un sextuple inverseur (6 portes Nand) à haute impédence d'entrée afin d'agir comme un buffer : le 74HCT04. Ce composant est capable de fournir l'intensité nécessaire à nos 5 LEDs,ces dernières étant en série avec des résistances adaptées.\\  
			Nous avons également inséré, avant et après l'alimentation, en parallèle, des condensateurs. Ceux-ci permettent de s'assurer que la tension est bien stable en supprimant les hautes fréquences. Etant donné que des intensités relativement élevées (dûes aux moteurs) seront mises en jeu, il est probable que des pics de tension apparaissent. Même si ce pic n'est pas démesuré, il pourrait tout de même endommagé la carte.\\

			Nous avons également décidé d'intégré un interrupteur à levier de type On/Off, afin d'économiser la batterie lorsque les moteurs ne sont pas nécessaires, et ainsi gagner en autonomie. Nous avons également inclu un bouton poussoir à impulsion (de type NO \nomenclature{NO}{Normally Open, Normalement ouvert}(On)/Off, selon les notations normalisées). Ce dernier démarrera la séquence de test, permettant ainsi de positionner le robot sur le circuit avant de commencer les tests.\\
			Les deux boutons sont accompagnés en dérivation de condensateurs. En effet, lors d'un changement d'état d'un interrupteur, le signal ne passe pas d'un état à un autre (de HAUT/HIGH à BAS/LOW ou inversement) immédiatement et parfaitement. Il y a une phase de transition qui, si elle n'est pas géré physiquement ou logiciellement, peut causer de graves problèmes, tel qu'un appui multiple, pouvant lancer plusieurs fois la séquence, entrainant des perturbations et pouvant potentiellement endommager le robot et/ou la carte. On parle de "debouncing", comme le présente la figure suivante :
			\begin{figure}[H]
				\centering
				\begin{subfigure}[h]{0.45\textwidth}
			        
			        \caption{Sans condensateur}D
			    \end{subfigure}
			    ~
			    \begin{subfigure}[h]{0.45\textwidth}
			        
			        \caption{Avec condensateur}
			    \end{subfigure}
			    \caption{Schéma de l'état d'un signal après l'ouverture d'un interrupteur}
			\end{figure}
			Grâce à ces schémas, on se rend rapidement compte de l'importance d'un simple composant passif. Dans le cas (a), le controlleur pourrait croire à de multiples pressions de l'interrupteur, pouvant engendrer des dommages au système mécanique, aussi bien qu'au système électrique. Dans le cas (b), le signal est continu et lissé. Il s'agit finalement d'un simple filtre passe-bas, puisqu'on a effacé toutes les hautes fréquences parasites.\\
			La carte mère est également pourvue d'un connecteur HE10-10, permettant une connexion simple et standard avec la carte réflecteurs. 
			\illu{he1010.jpg}{Connecteur femelle HE10-10 \textbf{\textit{(source : Conrad.fr)}}}{0.1}
			
			Le schéma de la Carte-mère a été réalisé grâce au logiciel Kicad, et est disponible en annexe, page \pageref{schemasCarteMere}.

		\paragraph{Structure du robot}

			L'intégration de tous les composants du robot passe forcément par un support, une structure d'ensemble.\\
			Nous avons choisi de réaliser cette structure sur une base de profilé aluminium de type "cornière égale" extrêmement simple à se procurer (dans toute enseigne de bricolage), peu chère, mais surtout très simple à usiner avec peu de matériel (l'aluminium étant très tendre, une simple visseuse suffit pour le perçage, une scie et une vis à métaux complétant l'outillage nécessaire).
			Un "cadre" en aluminium constituerai donc le châssis du robot. Ce cadre serait surmonté de quatre montants verticaux destinés à porter LEDs et caméra, et qui pourraient servir à fixer des "caches" pour fermer le robot (à la fois pour l'aspect esthétique et pour l'isolation lumineuse, afin de faciliter le travail de reconnaissance d'image). Un fond en médium ou en plexiglas abriterait le contrôleur et la batterie.\\

			L'idée maîtresse est de standardiser les matériaux et de penser au plus simple. Ainsi, nous essaierons tant que possible de tout faire avec un profilé aluminium unique (cornière égale de 30mm par 30mm), un seul type de vis et d'écrou (M3) et penserons notre assemblage de manière à être aisément réalisable, et ne présentant pas de risque de sur-contrainte.\\

			Le résultat vous est présenté à la section suivante : "Intégration globale, maquette numérique".

		\paragraph{Intégration globale, maquette numérique}

			Une maquette Catia nous a permis de définir le détail de la forme de la structure évoquée à la section précédente, mais également de prévoir l'intégration de tous les éléments.\\

			Tous les éléments de la maquettes ont été reproduits à partir des plans fournis par les constructeurs de composants sélectionnés. Ainsi, la maquette peut servir de plan d'usinage et de montage : aucune dimension n'est issue d'une quelconque approximation.

			\illu{ROBOT1.png}{Rendu de la maquette 3D du robot\label{robotVueExemple}}{0.4}
			\vspace{30pt}
			\illu{ROBOT2.png}{Rendu de la maquette 3D du robot}{0.4}

			\illu{ROBOT3.png}{Rendu de la maquette 3D du robot}{0.4}

			Le robot mesure 145mm de large (hors roues, 190 avec les roues), 200mm de long, et 150mm de haut.\\

			La maquette nous a permis d'évaluer le besoin en matériaux à :

			\begin{itemize}
				\item 1540mm de profilé aluminium.
				\item 4 vis M3 de 6mm de long.
				\item 24 vis M3 de 10mm de long (ou autant de vis auto-perçantes selon si l'on souhaite privilégier la facilité de fabrication ou la durée de vie).
				\item 10 vis M3 de 20mm de long.
				\item 34 écrous M3.
				\item 2 entretoises M3 de 15mm.
				\item 3 vis M2 de 10mm de long et autant d'écrous (pour le montage de la bille avant).
				\item une planche de medium de 3mm d'épaisseur en 140 par 200mm.
			\end{itemize}

	\subsubsection{Intégration Logicielle}\label{integrationLogicielle}

		L'intégration logicielle est sans aucun doute la partie la plus complexe de ce projet. Nous disposons d'un certain nombre d'entrées dont l'analyse simultanée permettra, au travers d'algorithmes relativement complexe, devra donner un ensemble de sorties cohérentes. Mais surtout, nous voulons que notre système soit modulaire, et que certaines parties de nos codes puissent être remplacés par d'autres, tout en assurant le fonctionnement des autres.\\

		Tout ceci ne pourra être effectué qu'au travers d'une architecture rigoureuse et largement pensée en amont (hors de question de se lancer dans le code comme on peut souvent le faire dans le cadre d'autres projets). Notons également que la construction d'une documentation et de codes clairement structurés et commentés sera également primordiale.\\

		Nous avons imaginé une structure en modules à quatre étages, au travers desquels l'information irait en descendant :

		\begin{itemize}
			\item \textbf{Les modules "Capteurs"} représenteraient le premier étage.\\
			Ces modules liraient directement la valeur des capteurs au travers des ports d'entrée physiques du contrôleur et produiraient une sortie adaptée.\\
			\textit{Par exemple, le module capteur" associé aux réflecteurs renverrait un vecteur de 7 bits correspondant à la présence ou non d'une ligne blanche sous chacun des capteurs : [1001001] correspondrait ainsi sans doute au passage d'un code barre. Plus compliqué, le module "capteur" associé à la caméra renverrait quatre matrices binaires 100x100 (une pour le vert, une pour le rouge, et une pour le jaune) dans lesquelles la présence d'un "1" indiquerait la détection d'une LED allumée aux cordonnées arrondies correspondantes.}
			\item \textbf{Les modules "Synthétiseur"} ne seraient pas liés à un capteur mais à une problématique. Ils pourront pour y répondre, analyser et synthétiser les données issues de plusieurs multiples modules capteurs.\\
			\textit{Ainsi, le synthétiseur lié à la problématique "lecture de codes barres" se renseignera auprès des modules capteurs "Réflecteurs optiques" et "Encodeur" afin de détecter la présence d'un code-barre et, le cas échéant, sa signification.}
			\item \textbf{Le module "Ordonnanceur"} serait a-priori unique. Il joue le rôle de chef d'orchestre et serait le seul module à intégrer la notion de temporalité (capacité de planification, et "mémoire" des événements récents). Ce serait également le seul module capable de faire "remonter de l'information" pour paramétrer le comportement des synthétiseurs.\\
			\textit{Par exemple, 25cm après la lecture d'un code-barre, l'ordonnanceur demanderait au synthétiseur dédié au suivi de ligne de ne plus se concentrer que sur une partie des réflecteurs optiques.}\\
			L'ordonnanceur fonctionnera forcément selon une logique séquentielle mais devra, pour être robuste et "clair", être décomposé en sous-modules (organe de décision, organe de planification, module dédié au gaz et module dédié à la direction, par exemple).
			\item \textbf{Les modules "Actionneurs"} recevraient des ordres (absolus ou relatifs) de la part de l'ordonnanceur et auraient pour rôle de les mettre en action au travers des sorties physiques du contrôleur.\\
			\textit{Concrètement, deux actionneurs géreront les sorties LEDs et les deux motoréducteurs. Un exemple "d'ordre absolu" pourrait-être "Vitesse = 0" tandis qu'un exemple d'ordre "relatif" serait "+5\% de rayon de virage".}
		\end{itemize}

		\vspace{15pt}

		Voici une simple illustration de la structure ici évoquée :
		\begin{figure}[H]
			\centering
			\input{Graphics/tikz/architectureLogicielle}
			\vspace{10pt}
			\caption{Structure logicielle en "modules"}
		\end{figure}

		Tous ces modules constitueraient l'un des livrables du projet et seraient codés en python, en suivant une approche "objet". A sa réception, le robot devra pouvoir être mis sous tension et évoluer en autonomie. Mais le réel enjeu du projet sera de faire en sorte que ces modules soient parfaitement documentés et architecturés, de manière à ce qu'un utilisateur souhaitant, par exemple, développer son propre module de reconnaissance d'image en C++ puisse faire fonctionner ce dernier avec le reste de nos modules (pour ne pas avoir à se préoccuper d'une partie suivi de ligne qui ne l 'intéresse pas).\\
		Ceci sera rendu possible, notamment, par l'utilisation optionnelle (mais intégrée) de sockets locaux UDP pour communiquer entre les modules.\\

		Un programme principal aurait pour rôle de gérer l’exécution des différents modules, et de répartir intelligemment leur utilisation processeur. Ce programme, lui même codé en python, sera conçu pour fonctionner nativement avec l'ensemble de nos modules, mais sera également capable d’exécuter des modules tiers. Ce programme devra lui-même faire preuve d'une très grande rigueur. Son fonctionnement sera régi par la lecture d'un fichier de configuration à son initialisation. Ainsi, ce fichier de configuration pourra déterminer quels modules devront-être exécutés, et avec quel paramétrage.\\

		Un scenario possible serait :\\
		\textit{Exécuter tous les modules natifs sauf le module synthétiseur spécialisé en reconnaissance de feux qui sera remplacé par le programme "monProgramme.exe" placé à la racine. Le module capteur "sonar" devra communiquer sur le port 40052. Les autres modules seront chargés en configuration par défaut.}\\
		Ces instructions seraient définies dans le fichier de configuration, et leur exécution serait assurée par le programme principal. Évidemment, ceci ne pourra fonctionner que si l'utilisateur a très soigneusement suivi les recommandations de la documentation lui indiquant quel type de données doit fournir le module synthétiseur spécialisé en reconnaissance de feux.\\

		Encore une fois, rien n'obligera l'utilisateur à se servir de cette base logicielle. Il pourra très bien décider d'ignorer totalement le système en place et concevoir le sien. Le but de ce système est vraiment de permettre à un élève de se concentrer sur une problématique ciblée en voyant les autres traitées pour lui. Mais cela ne peut se faire que si son propre module n'empêche pas le fonctionnement des autres. Ceci ne peut être le cas que si son module est parfaitement additionnel (et fait donc un travail dont le résultat n'est requis par aucun autre module) ou si il est parfaitement compatible avec les autres (et transmet donc les données dans le même format et selon le même protocole que le module natif).\\

		Nous ne pouvons pas insister suffisemment sur le fait que ceci ne représente que l'approche théorique du problème. Si nous l'avons longuement pensé et réfléchi, ce travail n'est absolument pas suffisent pour donner lieu à une phase de développement : celle-ci devra être précédée d'une phase de préparation minutieuse, notemment en utilisant les outils de "Model Driven Engineering" (diagrames de classes, d'interaction...) afin de mettre en place un cadre de travail strict et rigoureux absolument nécéssaire à la réussite d'un projet de ce type.

\subsection{Synthèse}
	Pour mieux se représenter le système dans son ensemble, voici quelques mises en situation :\\
	\illu{miseEnSituation.png}{Mise en situation du robot sur le circuit}{0.5}
	\vspace{25pt}
	\illu{miseEnSituation1.png}{Mise en situation du robot sur le circuit}{0.5}
	\illu{miseEnSituation2.png}{Mise en situation du robot sur le circuit}{0.5}

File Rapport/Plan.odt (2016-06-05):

I. Introduction
II. Définition du besoin
  1. Support de TP
  2. Outil de recherche
III. Étude du besoin
  1. Analyse du besoin
    Quelles sont les implications/contraintes ?
    Choix des lignes directrices du projet : partie direction et gaz séparées, technos utilisées…
  2. Use case diagrams
  3. Décomposition de la problématique
    a. Lignes blanches
    b. Feux synchronisés
    c. Détection de présence
    d. Simplicité d’utilisation :
      i. Deux parties pour stockage
      ii. Facilement et rapidement assemblables
      iii. Carte et connecteurs adaptés
    e. Suivi de ligne
    f. Détection des feux et autres véhicules
    g. Logiciellement modulaire
    h. Problématiques matérielles : autonomie, type de propulsion/direction… Utilisation des « expériences » passées
IV. Élaboration d’une solution
  1. Feux synchronisés
    a. Utilisation FPGA
    b. Feux bicolores à LED 5mm
  2. Détection de présence
    a. Choix du type de capteur
    b. Implémentation (sur circuit, sur robots, sur FPGA)
  3. Simplicité d’utilisation
    a. Catia du circuit
    b. Câblage, carte, connecteurs
  4. Suivi de lignes

Incrémentation successive de la problématique jusqu’à solution finale

Nouvelle contrainte sur le circuit => codes barres

  1. Détection des feux et autres véhicules

Incrémentation successive de la problématique jusqu’à solution finale

+ notion de découpage binaire d’un comportement instinctif

Nouvelle contrainte sur le circuit => isolation visuelle

  1. Implémentation logicielle
    a. Choix de la structure
    b. Diagramme des classes
    c. Interface de mise à jour/paramétrage des codes
  2. Implémentation matérielle
    a. Choix du type de propulsion/direction
    b. Choix des actionneurs
    c. Choix des éléments de structure
    d. Choix de la batterie
    e. etc...
V. Intégration
  1. Catia du robot
  2. Catia final du circuit
  3. Choix et explication du cycle de développement
    Ce dossier a pris en charge la partie descendante du cycle en V. Reste partie ascendante (PFE?). Choix d’une montée incrémentale :
    Pour logiciel comme pour circuits : fonctionnalité de base => test => ajout d’une fonctionnalité => test…
    Donner le détail des étapes et des procédures de validation avec estimation horaire
VI. Estimation du coût de mise en place et faisabilité
  1. Devis matériel
  2. Détail des équipements et infrastructures nécéssaires
  3. Diagramme de Gant
VII. Conclusion et aperçu des évolutions possibles
VIII. Annexes
  1. Catias
  2. Circuits électroniques
  3. Devis détaillés
  4. Logigrames

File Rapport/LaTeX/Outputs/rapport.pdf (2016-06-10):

## Projet Electif

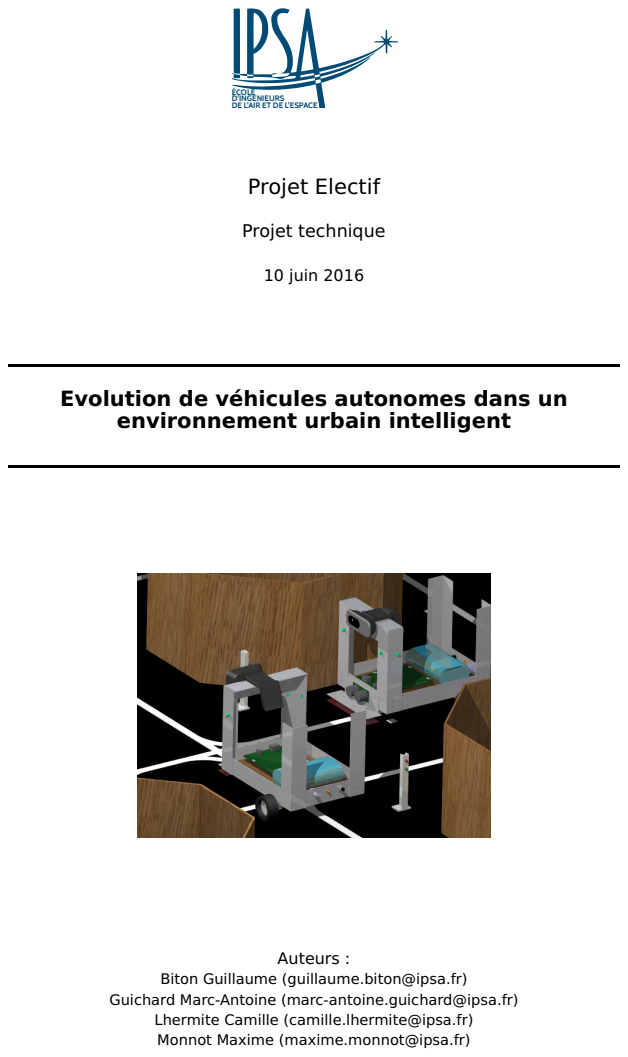
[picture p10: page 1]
Projet technique; 10 juin 2016; Auteurs :

ÉCOLE D'INGÉNIEURS
DE L'AIR ET DE L'ESPACE

Evolution de véhicules autonomes dans un
environnement urbain intelligent

Biton Guillaume (guillaume.biton@ipsa.fr)

Guichard Marc-Antoine (marc-antoine.guichard@ipsa.fr)

Lhermite Camille (camille.lhermite@ipsa.fr)
Monnot Maxime (maxime.monnot@ipsa.fr)

# Table des matières

1 Introduction | 2
2 Définition du besoin | 3
3 Étude du besoin | 5
4 Élaboration d’une solution | 11
5 Intégration | 35

6 Estimation du coût de mise en place et faisabilité | 47
7 Suivi de projet | 50
8 Conclusion et aperçu des évolutions possibles | 51
Annexes | 52
Références | 64
Résumé | 68

# Remerciements

Nous remercions Mesdames Assia Belbachir et Sorore Benabid, ensignants cher-

cheurs au sein du laboratoire Mécatronique, Signal et Systèmes de l’IPSA pour nous

avoir soumis cette idée, pour nous avoir accordé leur confiance quant à sa réalisa-

tion potentielle et pour leur soutien dans le cadre de ce projet.

# Notes préliminaires

L’ensemble des illustrations présentes dans ce dossier, sauf indication contraire

dans leurs légendes, sont des réalisations personnelles et ne sont donc soumises à

aucun droit particulier.

Le travail de recherche ici présenté est sous la responsabilité des auteurs cités en

première de couverture et sous la propriété de l’IPSA. Merci de nous contacter au

moyen des adresses fournies pour nous signaler tout problème, ou pour toute de-

mande liée à l’utilisation du contenu.

L’ensemble des abréviations utilisées dans ces pages sont explicitées en page 64

(nomenclature).

Les numéros entre crochets pouvant apparaitre au sein de paragraphes sont des

références bibliographiques et vous renvoient à la page 65 (bibliographie).

Ce dossier comprend de nombreuses références dynamiques, et pour un confort

de lecture optimal, nous vous conseillons d’en lire la version numérique afin de

pouvoir bénéficier des liens cliquables.

Exception faite des modèles mécaniques en CAO 3D effectués sous Catia®, l’en-

semble des réalisations ici présentées utilisent des outils Open-Source : le présent

dossier est rédigé en LATEX, (https://www.latex-project.org/) les illustrations ont été réalisées en dessin-vectoriel sous

Inkscape (https://inkscape.org/fr/) ou en matriciel sous GIMP (https://www.gimp.org/) et les schémas et circuits électroniques sous Ki-

Cad. (http://kicad-pcb.org/)

# 1 Introduction

La voiture autonome, loin du concept de science-fiction qu’elle pouvait représenter

il y a quelques années est en train de devenir une réalité.

Si cette ambition put être à une certaine époque motivée par le simple attrait

de la prouesse technique, nous percevons aujourd’hui tous les bénéfices que l’on

pourrait en tirer. En effet, les avancées scientifiques et techniques nous permettent

désormais de prétendre à concevoir une voiture qui soit non seulement autonome,

mais surtout intelligente. Il est aujourd’hui tout à fait réaliste de penser que dans

les quelques années à venir les voitures sauront adopter un comportement bien

plus intelligent que celui de leurs conducteurs actuels, et ce au profit de la sécurité,

de l’ efficience énergétique mais également de l’encombrement des axes routiers.

A terme, nous pouvons facilement imaginer que les différents véhicules auront la

possibilité de communiquer entre eux afin de prévenir les véhicules environnants

de leurs intentions, mais cela ne les dispensera pas de devoir être capables d’éva-

luer leur environnement afin d’y détecter les éléments "indépendants" (piétons,

obstacles...).

Comme toute révolution technologique, la voiture intelligente devra faire face au

caractère progressif de son adoption : toutes les voitures sur les routes ne devien-

dront pas autonomes du jour au lendemain. Ces véhicules devront donc également

être capables d’évoluer au milieu d’une circulation telle que nous la connaissons,

où chaque acteur adopte un comportement presque parfaitement aléatoire, et ne

signale pas toujours ces intentions.

Si les voitures deviennent intelligentes, c’est également le cas, depuis quelques

années déjà, de la signalisation. Ainsi, de plus en plus de feux adaptent leur com-

portement au trafic, ce qui s’inscrit également dans une démarche d’optimisation

de la circulation. Il est très réaliste d’espérer que cette technologie déjà existante

se fera omniprésente dans les années qui viennent, d’où notre volonté d’inclure cet

élément d’environnement à notre projet.

Le but de ce projet est donc d’étudier notre capacité à faire cohabiter intelligence

artificielle et environnement "réel" et indépendant avec des moyens techniques et

financiers extrêmement restreints, mais également et surtout de fournir une pla-

teforme d’expérimentation aux étudiants de l’IPSA (et d’ailleurs ?) afin de faciliter

l’apprentissage des sciences de la mécatronique et de l’intelligence artificielle tout

en ancrant ce savoir dans une réalité pratique et stimulante.

# 2 Définition du besoin

Une définition pertinente du besoin est une condition absolument nécessaire pour

la bonne réalisation de tout projet. Nous nous emploierons donc à définir aussi

précisément et pertinemment que possible le besoin motivant ce projet, et à régu-

lièrement revenir sur ce dernier afin de prendre en compte d’éventuelles évolutions

et à prévenir toute dérive du projet.

## 2.1 Besoin

Le besoin à l’origine de ce projet fut exprimé par mesdames A. Belbachir et S.

Benabid en tant qu’enseignants chercheurs au laboratoire Mécatronique, Signal et

Systèmes à l’IPSA. Leur souhait était de bénéficier d’une plateforme articulée au-

tour de robots autonomes évoluant dans une simulation d’environnement urbain,

capables de détecter des feux de signalisation "intelligents" et d’adapter leur com-

portement en conséquence. Cette plateforme pourrait servir de support de TP dans

l’ensemble des matières enseignées par le département, mais également servir de

"vitrine" voir même de plateforme de recherche.

Les principales fonctionnalités évoquées étant :

— La reconnaissance d’image pour la détection des feux de signalisation.

## — La présence de feux bicolores commandés par FPGA. Ces feux seraient

"intelligents" dans le sens où il s’adapteraient à la circulation. La présence de

capteurs de présence est donc induite.

## 2.2 Précision du besoin

Ayant suivi nombre de matières enseignées par le département et participé à de

nombreuses séances de travaux pratiques, nous bénéficions d’une image relative-

ment claire des implications de ce projet ainsi que des contraintes relevant pour la

plupart du simple bon sens. Dans un soucis de clarté et d’application de "bonnes

pratiques" nous prîmes cependant soin de valider l’ensemble de ces éléments au

cours de réunions avec nos "clients" du laboratoire.

Ainsi, nous ajoutâmes les points suivants à la liste des exigences :

— "Côté circuit" :
— Le circuit devra bénéficier d’un encombrement raisonnable.

## — Les feux de circulation devront pouvoir être commandés via une

carte FPGA.

— "Côté robots" :

## — Les robots devront pouvoir être utilisés en classe sans que les pré-

occupations matérielles ne soient accaparantes.

## — Les robots devront pouvoir être programmés en utilisant les lan-

gages enseignés à l’IPSA à savoir C et C++ et ses variantes (Arduino...),

Python, voir même Matlab...

## — Les robots devront bénéficier de possibilités d’application flexibles :

les enseignements étant ciblés, il est important que les utilisateurs des ro-

bots puissent se concentrer sur un aspect de leur utilisation sans avoir à se

soucier des autres. De même, les robots devront embarquer suffisamment

de capteurs ou tout du moins de capacité d’extensions pour que cela ne soit

pas un facteur limitant lors de l’élaboration de sujets de TP.

## — Les robots devront ne pas pouvoir représenter un danger pour ses

utilisateurs.

# 3 Étude du besoin

## 3.1 Analyse du besoin

Le besoin exprimé précédemment comporte un certain nombre d’implications lo-

giques. Leur prise en compte relève déjà du domaine de la solution, mais reste

d’ordre suffisamment général pour être évoquée ici. Surtout, ces points seront à

prendre en compte lors de l’élaboration d’une solution "détaillée".

Reprenons les points évoqués ci-avant :

## 3.1.1 Pour le circuit

- Le circuit devra bénéficier d’un encombrement raisonnable.

⇒ Les dimensions du circuit devront être raisonnables.

⇒ Nous songerons également à une structure démontable (qui devra rester

simple à assembler).

## - Les feux de circulation devront pouvoir être commandés via une carte

FPGA.

⇒ Une carte adaptant les tensions et courants et disposant de connecteurs

adaptés aux caractéristiques des cartes possédées par l’IPSA devra être pro-

posée.

⇒ La carte FPGA aura pour rôle de synchroniser les feux.

⇒ La carte FPGA pourra tirer partie de capteurs de présence par adapter le

cycle des feux.

## 3.1.2 Pour le robot

## - Les robots devront pouvoir être utilisés en classe sans que les préoc-

cupations matérielles ne soient accaparantes.

⇒ Cela implique plusieur points :

- Bénéficier d’une autonomie suffisante pour que l’ensemble des groupes

puissent effectuer leurs manipulations au cours d’une séance entière sans

que cela ne nécéssite de charger/remplacer la batterie. D’expérience,

nous estimons l’autonomie minimum à une heure pour répondre à ce cri-

tère.

- Présenter des connecteurs et des interfaces permettant une intéraction

"technique" avec le robot ne nécessitant pas de matériel complexe. Ceci

passe par la possibilité de changer ou recharger la batterie sans outils

particuliers, de pouvoir programmer le robot via USB ou réseau plutôt

que via un port parallèle par exemple, ou encore proposer au minimum

un bouton accessible permettant le lancement d’un séquence de code

prédéfinie.

- Etre d’une conception suffisamment robuste pour pouvoir être manipulé

quotidiennement sans en "souffrir" et suffisamment simple pour pouvoir

être aisément entretenu.

## - Les robots devront pouvoir être programmés en utilisant les langages

enseignés à l’IPSA.

⇒ Cette problématique sera étudiée plus en détail en 4.2.3.2 (page 22)
- Les robots devront bénéficier de possibilités d’application flexibles.

⇒ Ceci passe par une modularité totale des différents éléments qui com-

posent le robot, aussi bien sur le plan matériel que logiciel. Cette modularité

devra rester une préoccupation de premier plan tout au long du développe-

ment de ce projet.
- Les robots devront ne pas représenter de danger pour ses utilisateurs.

⇒ La structure du robot ne devra pas présenter d’éléments tranchants.

⇒ La partie électrique et électronique devra employer des puissances raison-

nables, et être protégée contre les forts courants.

## 3.2 Diagrammes des cas d’utilisation

Toujours dans un soucis de clareté et de bonne pratiques, nous avons ébauché les

diagrammes des cas d’utilisation de haut niveau suivants :

## 3.2.1 Pour le circuit

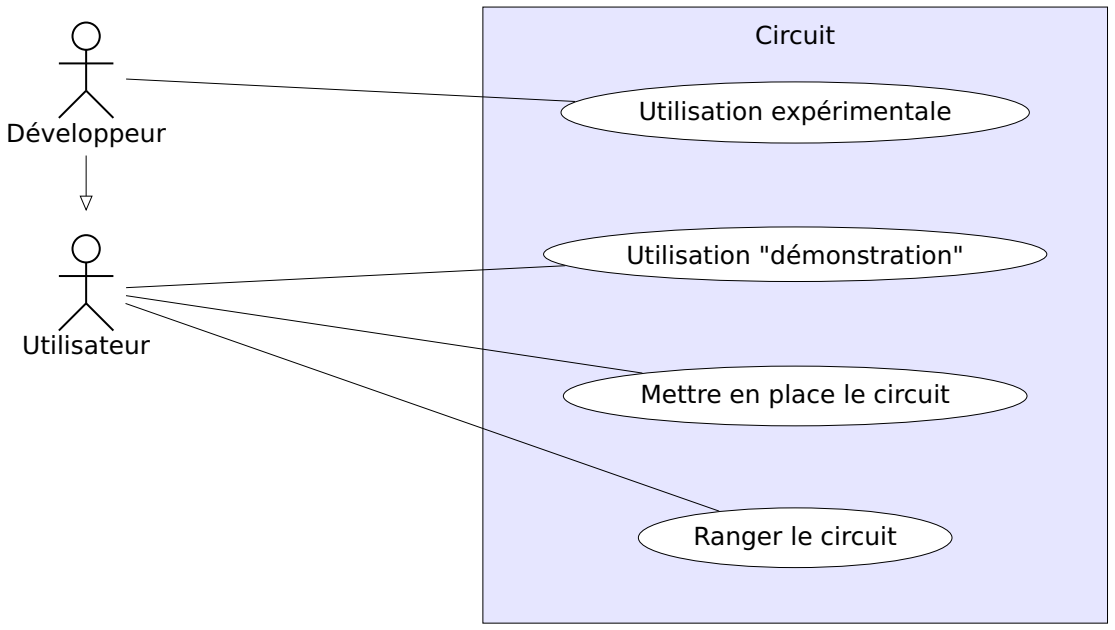
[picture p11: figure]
Circuit; Utilisation expérimentale; Utilisation "démonstration"; Mettre en place le circuit; Ranger le circuit; Développeur; Utilisateur

## Utilisation expérimentale

- Précondition : Le circuit est en place. L’utilisateur dispose d’une carte FPGA

programmée et alimentée.

- Déclencheur : Un utilisateur souhaite tester son programme VHDL

## - Scenario :

1. L’utilisateur connecte sa carte FPGA à la carte du circuit en veillant à respec-

ter les branchements.

2. L’utilisateur effectue les tests et observations qu’il désire.

3. L’utilisateur déconnecte sa carte FPGA.

## Utilisation "démonstration"

- Précondition : On dispose d’une carte programmée pour la demonstration.
- Déclencheur : Un utilisateur souhaite effectuer une démonstration.

## - Scenario :

1. L’utilisateur connecte la carte FPGA de démonstration à la carte du circuit en

veillant à respecter les branchements.

2. L’utilisateur alimente la carte FPGA de démonstration.
3. L’utilisateur laisser le système évoluer en autonomie.
4. L’utilisateur coupe l’alimentation de la carte FPGA de démonstration.
5. L’utilisateur déconnecte laa carte FPGA de démonstration.

## Mettre en place le circuit

- Précondition : On dispose es éléments du circuit et de la place nécéssaire à

son installation
- Déclencheur : Un souhaite utiliser le circuit qui n’est pas déjà en place

## - Scenario :

1. L’utilisateur s’assure que les deux parties sont en état d’être assemblées.
2. L’utilisateur isole les deux faisceaux de câbles.
3. L’utilisateur assemble les deux parties du circuit.
4. L’utilisateur vérouille les deux parties du circuit.
5. L’utilisateur installe les feux à leurs emplacements et les connecte à leurs

faisceaux de câbles.

6. L’utilisateur installe les différents "caches".
7. L’utilisateur branche les deux faisceaux de câbles à leurs connecteurs sur la

carte du circuit.

## Ranger le circuit

- Précondition : Le circuit est installé et n’est pas en cours d’utilisation.
- Déclencheur : Un ne se sert pas du circuit et on souhaite libérer la place.

## - Scenario :

1. L’utilisateur déconnecte les deux faisceaux de câbles de la carte du circuit.
2. L’utilisateur retire les différents "caches".
3. L’utilisateur déconnecte les feux de leurs faisceaux de câbles et les retire de

leurs emplacements.

4. L’utilisateur dévérouille les deux parties du circuit.
5. L’utilisateur s’assure que les deux parties sont en état d’être manipulées et

déplacées.

6. L’utilisateur range les deux parties du circuit.

## 3.2.2 Pour le robot

## Reprogrammation :

- Précondition : Nous disposons d’un programme fonctionnel.
- Déclencheur : Un développeur souhaite implémenter un programme.

## - Scenario :

1. On connecte le robot à une source de tension.
2. On établit une liaison entre le robot et un ordinateur.
3. Le développeur lance le téléversement du programme.
4. Le robot acquitte.
5. On ferme la connexion.

## Evolution en autonomie :

- Précondition : Le robot a été programmé et dispose d’une batterie chargée.
- Déclencheur : Un membre du laboratoire souhaite observer le comportement

du robot.

## - Scenario :

1. On met le robot sous tension.
2. On place le robot sur une ligne blanche du circuit.
3. On appuie sur le bouton de démarrage de séquence
4. Le robot déclenche les programmes en mémoire.

## Changement de batterie :

- Déclencheur : On souhaite changer la batterie du robot

## - Scenario :

1. On met le robot hors tension.
2. On accède à la batterie en place le cas échéant, et on la retire.
3. On met en place la nouvelle batterie
4. On remet en place les éléments éventuellement retirés pour accéder à la

batterie.

Le mode d’utilisation primaire est bien évidemment celui de l’évolution en auto-

nomie. Le robot étant destiné à servir de plateforme de recherche, et devant donc

être entièrement reprogrammable, il est délicat de décrire ce mode d’utilisation qui

dépendra intégralement du programme chargé par l’utilisateur.

Nous nous appliquerons cependant à décrire le mode d’utilisation correspondant à

l’application la plus basique du robot (et de fait au programme que nous livrerons

avec ce dernier).

# 4 Élaboration d’une solution

## 4.1 Circuit

## 4.1.1 Structure

Le circuit sera principalement composé de medium de 5mm d’épaisseur (maté-

riau résistant, léger, peu fragile, facilement usinable et peu cher) reposant sur une

structure une taseaux (de manière à surelever le plateau, afin de passer les câbles

en dessous et laisser de la place pour les systèmes de fixation, par exemple ainsi

que pour rigidifier la structure (le medium étant un matériau souple)).

Nous avons décidé de donner à la "piste" du circuit la forme suivante :

Figure 1 – Forme de la "piste" du circuit

Ainsi, nous avons un carrefour à feux ainsi que quatre intersections, soit un large

éventail de possibilités.

Après avoir fait une rapide estimation des dimensions de notre robot, nous avons

déduit que le circuit devrait faire environ deux mètres par deux mètres. Nous avons

préféré ajouter vingt centimètres de côté par sécurité.

Ces dimensions étant importantes, ceci nous a conforté dans l’idée que notre cir-

cuit devrait être fait en deux parties afin d’en faciliter le rangement. Nous fabrique-

rions donc deux cadres de deux mètres vingt par un mètre dix qui pourront être

facilement assemblés.

## 4.1.2 Feux

Les feux seront comprendront chacun deux LED "haute luminosité" de 5mm : une

rouge et une verte. Trois fils seront donc nécéssaires pour chaque feu : deux pour

les alimentations de chacune des LEDs et une masse commune. Avec les quatre

feux, le circuit comptera donc huit LEDs et douze fils différents.

Les feux seront dans la mesure du possible imprimés en 3D :

Figure 2 – Maquette numérique d’un feu bicolore

Notons la présence de deux petits trous pour enficher les feux sur des vis et d’un

plus gros pour le passage des fils. Un passe-câble est également intégré à la "gou-

lotte" qui constitue le montant du feu afin de guider les fils.

## 4.1.3 Capteurs

Afin d’adapter le comportement des feux à l’état du trafic, encore faut-il que la

carte FPGA dispose d’un moyen d’évaluer ce trafic.

Nous disposerons donc sur la piste des capteurs "ILS" (Interrupteur à Lame Souple)

sur la piste aux abords des feux. Les ILS sont de petits composants se comportant

comme un interrupteur ouvert en temps normal, et comme un interrupteur fermé

lorsqu’on approche un aimant.

En munissant nos robots d’un aimant bien placé, ces derniers fermeront temporai-

rement le circuit lors de leur arrivée aux abords des feux.

Cette solution est extremement simple et ne nécéssite aucun traitement du signal

(contrairement aux capteurs à effet hall ou fourches optiques, souvent utilisés en

détection de présence).

## 4.2 Robot
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

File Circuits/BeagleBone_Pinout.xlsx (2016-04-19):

PORT | Pin | Usage | Name
P8 | 1 | POW | GND
 | 2 | POW | GND
 | 3 | D | GPIO_38
 | 4 | D | GPIO_39
 | 5 | D | GPIO_34
 | 6 | D | GPIO_35
 | 7 | D | GPIO_66
 | 8 | D | GPIO_67
 | 9 | D | GPIO_69
 | 10 | D | GPIO_68
 | 11 | D | GPIO_45
 | 12 | D | GPIO_44
 | 13 | PWM | EHRPWM2B
 | 14 | D | GPIO_26
 | 15 | D | GPIO_47
 | 16 | D | GPIO_46
 | 17 | D | GPIO_27
 | 18 | D | GPIO_65
 | 19 | PWM | GPIO_22
 | 20 | D | GPIO_63
 | 21 | D | GPIO_62
 | 22 | D | GPIO_37
 | 23 | D | GPIO_36
 | 24 | D | GPIO_33
 | 25 | D | GPIO_32
 | 26 | D | GPIO_61
 | 27 | D | GPIO_86
 | 28 | D | GPIO_88
 | 29 | D | GPIO_87
 | 30 | D | GPIO_89
 | 31 | D | GPIO_10
 | 32 | D | GPIO_11
 | 33 | D | GPIO_09
 | 34 | D | GPIO_81
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

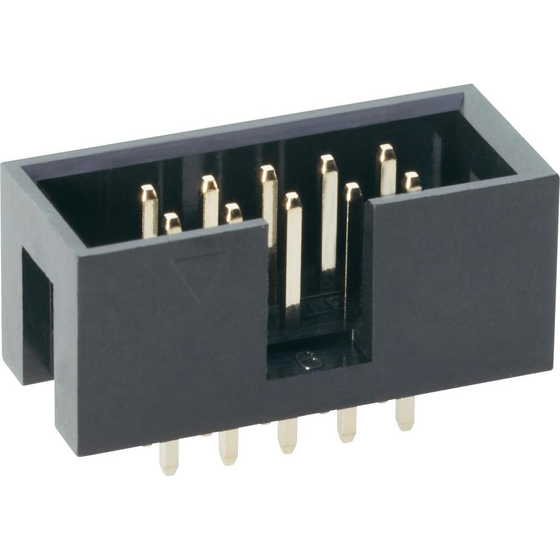
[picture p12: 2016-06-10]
Rapport/LaTeX/Graphics/he1010.jpg

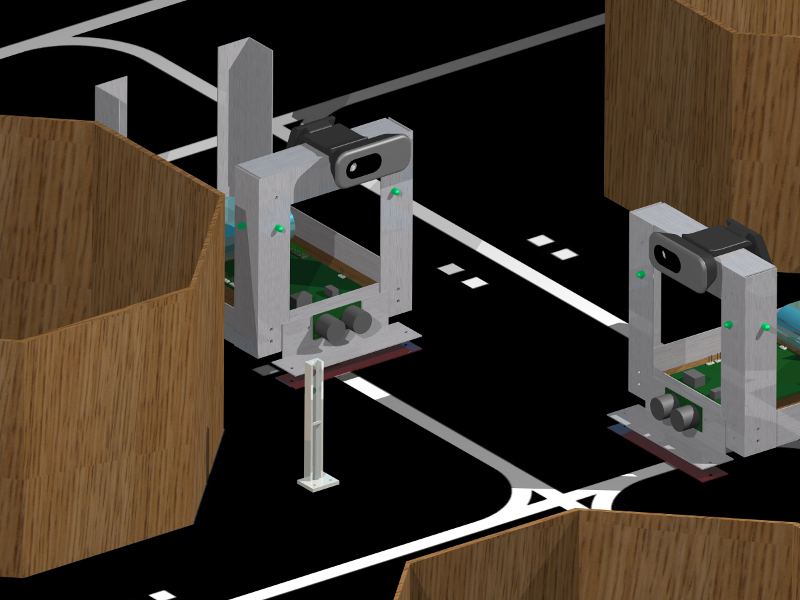
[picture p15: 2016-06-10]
Rapport/LaTeX/Graphics/miseEnSituation2.png

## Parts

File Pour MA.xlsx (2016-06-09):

# | Tâche | Durée | Nombre de personnes | Heures-homme | Nécessite | Package | Remarque
1 | Commande des pièces et composants + livraison | 10.0 j | 1 | 2 | - | Fournitures | Peu d’heures-homme : surtout du temps d’attente !!!
2 | Test des cicuits électroniques sur Breadboard | 0.5 j | 2 | 8 | 1 | Réalisation cartes
3 | Réalisation des circuits imprimés | 1.0 j | 2 | 16 | 2
4 | Intégration des composants sur les CI | 0.5 j | 2 | 8 | 3
5 | Test des CI | 0.2 j | 1 | 2 | 4 |  | JALON
6 | Usinage profilés alu | 1.0 j | 2 | 16 | 1 | Assemblage robot
7 | Assemblage du robot | 1.0 j | 2 | 16 | 6
8 | Câblage, sertissage et branchement des périphériques | 0.5 j | 1 | 4 | 5.7
9 | Tests électrique du robot | 0.2 j | 1 | 2 | 8 |  | JALON
10 | Réalisation des feux en impression 3D | 2.0 j | 1 | 3 | - | Réalisation circuit | Peu d’heures-homme : surtout du temps d’utilisation machine !!!
11 | Usinage pièces bois | 0.5 j | 2 | 8 | 1
12 | Assemblage du circuit | 0.5 j | 2 | 8 | 11
13 | Peinture circuit | 0.5 j | 1 | 4 | 12
14 | Tracé des lignes | 1.0 j | 1 | 8 | 13
15 | Câblage et sertissage connecteurs | 0.5 j | 1 | 4 | 12
16 | Test du circuit | 0.2 j | 1 | 2 | 15 |  | JALON
17 | Mise en place de l’environnement logiciel sur le BBG (OS, réseau…) | 1.0 j | 1 | 8 | 1 | Développement logiciel | Toutes ces étapes pourraient être subdivisées en nombreuses sous-étapes : le développement de chaque module étant décomposeable en de nombreuses itérations partant de la structure la plus basique et allant jusqu’au module complet via de nombreuses « couches » successives. Le nombre de tests est ici bien trop important pour que ces derniers soient mentionné.
18 | Développement des modules capteurs | 0.2 j | 1 | 2 | -
19 | Développement du module de synthèse « codes-barres » | 0.2 j | 1 | 2 | 18
20 | Développement du module de synthèse « suivi de ligne » | 0.2 j | 1 | 2 | 18
21 | Développement du module de synthèse « Détection de feux » | 3.0 j | 1 | 24 | 18
22 | Développement du module de synthèse « Détection autres véhicules » | 3.0 j | 1 | 24 | 18
23 | Développement de l’ordonnanceur | 5.0 j | 2 | 80 | 19,20, 21,22
24 | Développement du programme principal | 5.0 j | 2 | 80 | - |  | EN PARALLÈLE DE TOUT LE RESTE
25 | Construction de la documentation | 3.0 j | 2 | 48 | - | Documentation | EN PARALLÈLE DE TOUT LE RESTE
26 | Essai globaux et corrections | 4.0 j | 2 | 64 | TOUT |  | JALON
TOTAL |  | 45.0 j |  | 445

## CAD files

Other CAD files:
CATIA V2/CIRCUIT/CIRCUIT.CATProduct
CATIA V2/CIRCUIT/ENSEMBLE_FEU.CATProduct
CATIA V2/CIRCUIT/Ensemble.CATProduct
CATIA V2/CIRCUIT/LED.CATPart
CATIA V2/CIRCUIT/Panneau.CATProduct
CATIA V2/CIRCUIT/Panneau1.CATPart
CATIA V2/CIRCUIT/TOTAL.CATProduct
CATIA V2/CIRCUIT/Tasseau_court.CATPart
CATIA V2/CIRCUIT/Tasseau_long.CATPart
CATIA V2/CIRCUIT/Tasseau_med.CATPart
CATIA V2/CIRCUIT/cache - Copie.CATPart
CATIA V2/CIRCUIT/cache.CATPart
CATIA V2/CIRCUIT/feu.CATPart
CATIA V2/CIRCUIT/plateau.CATPart
CATIA V2/MISE EN SCENE.CATProduct
CATIA V2/ROBOT/BBG/BBG.CATPart
CATIA V2/ROBOT/BBG/BBG_Cap.CATPart
CATIA V2/ROBOT/BBG/BBG_Product.CATProduct
CATIA V2/ROBOT/BBG/con4.CATProduct
CATIA V2/ROBOT/BBG/connecteur1.CATPart
CATIA V2/ROBOT/BBG/connecteur2.CATPart
CATIA V2/ROBOT/BBG/connecteur3.CATPart
CATIA V2/ROBOT/BBG/connecteur3.CATProduct
CATIA V2/ROBOT/BBG/connecteur4.CATPart
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

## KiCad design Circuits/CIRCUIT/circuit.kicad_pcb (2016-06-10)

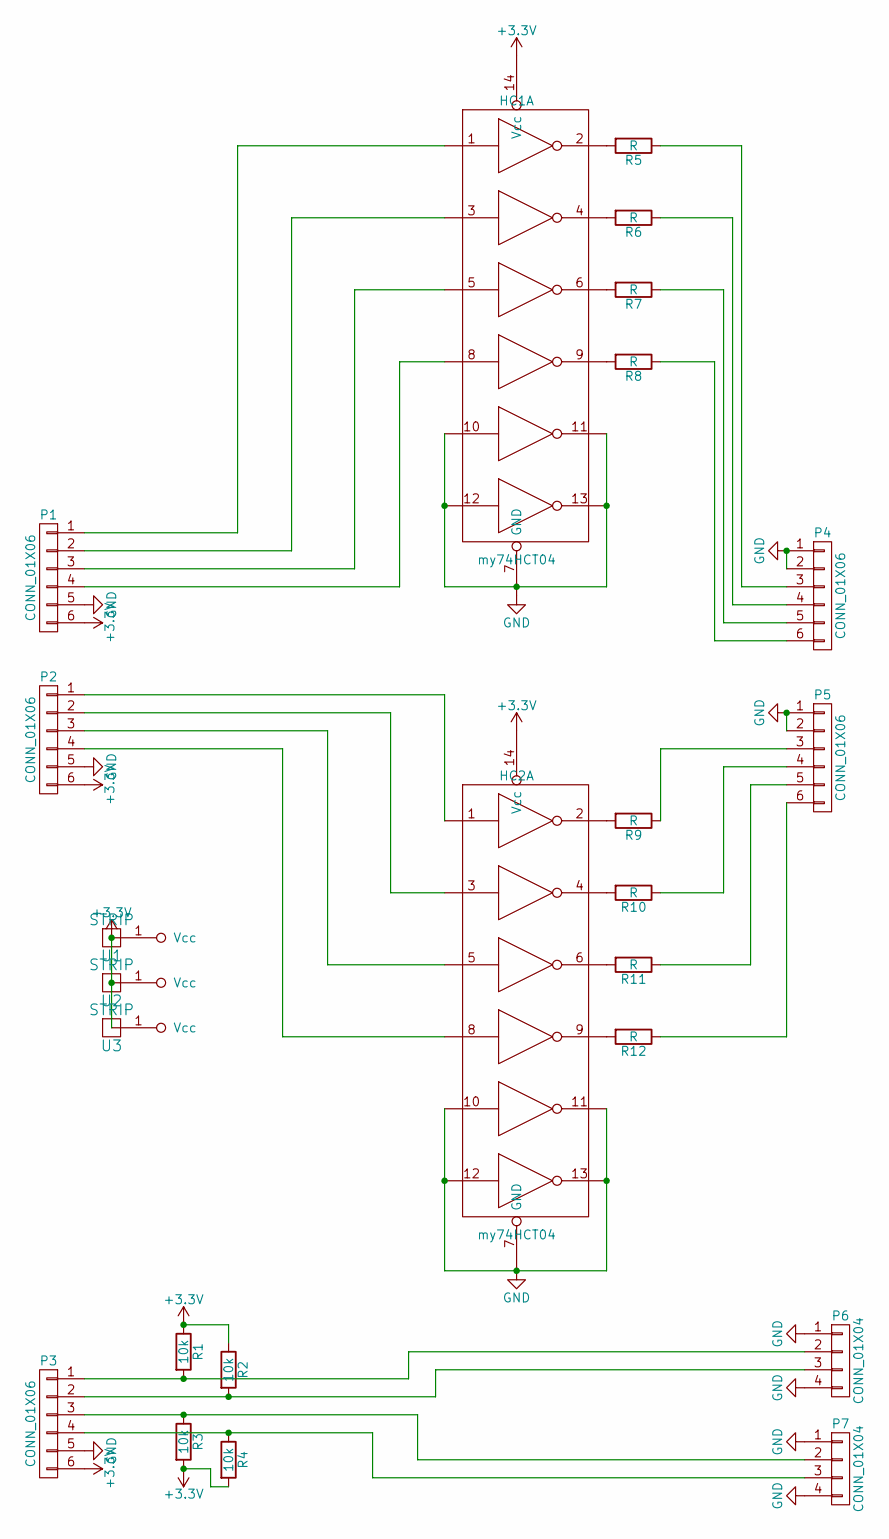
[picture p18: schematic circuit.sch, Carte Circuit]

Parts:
HC1, HC2: my74HCT04; DIP-14_W7.62mm
P1, P2, P3, P4, P5: CONN_01X06; Pin_Header_Angled_1x06
P6, P7: CONN_01X04; Pin_Header_Straight_1x04
R1, R2, R3, R4: 10k; Resistor_Horizontal_RM7mm
R5, R6, R7, R8, R9, R10, R11, R12: R; Resistor_Horizontal_RM7mm
U1, U2, U3: STRIP; SolderWirePad_2x_1-2mmDrill

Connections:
GND: HC1.7 (GND), HC2.7 (GND), HC2.10, HC2.11, HC2.12, HC2.13, P1.5, P2.5, P3.5, P4.1, P4.2, P5.1, P5.2, P6.1, P6.4, P7.1, P7.4
unnamed: HC1.1, P1.1
unnamed: HC1.2, R5.2
unnamed: HC1.3, P1.2
unnamed: HC1.4, R6.2
unnamed: HC1.5, P1.3
unnamed: HC1.6, R7.2
unnamed: HC1.8, P1.4
unnamed: HC1.9, R8.2
unnamed: HC1.10, HC1.11, HC1.12, HC1.13
unnamed: HC2.1, P2.1
unnamed: HC2.2, R9.2
unnamed: HC2.3, P2.2
unnamed: HC2.4, R10.2
unnamed: HC2.5, P2.3
unnamed: HC2.6, R11.2
unnamed: HC2.8, P2.4
unnamed: HC2.9, R12.2
unnamed: P3.1, P6.2, R1.2
unnamed: P3.2, P6.3, R2.2
unnamed: P3.3, P7.2, R3.1
unnamed: P3.4, P7.3, R4.1
unnamed: P4.3, R5.1
unnamed: P4.4, R6.1
unnamed: P4.5, R7.1
unnamed: P4.6, R8.1
unnamed: P5.3, R9.1
unnamed: P5.4, R10.1
unnamed: P5.5, R11.1
unnamed: P5.6, R12.1

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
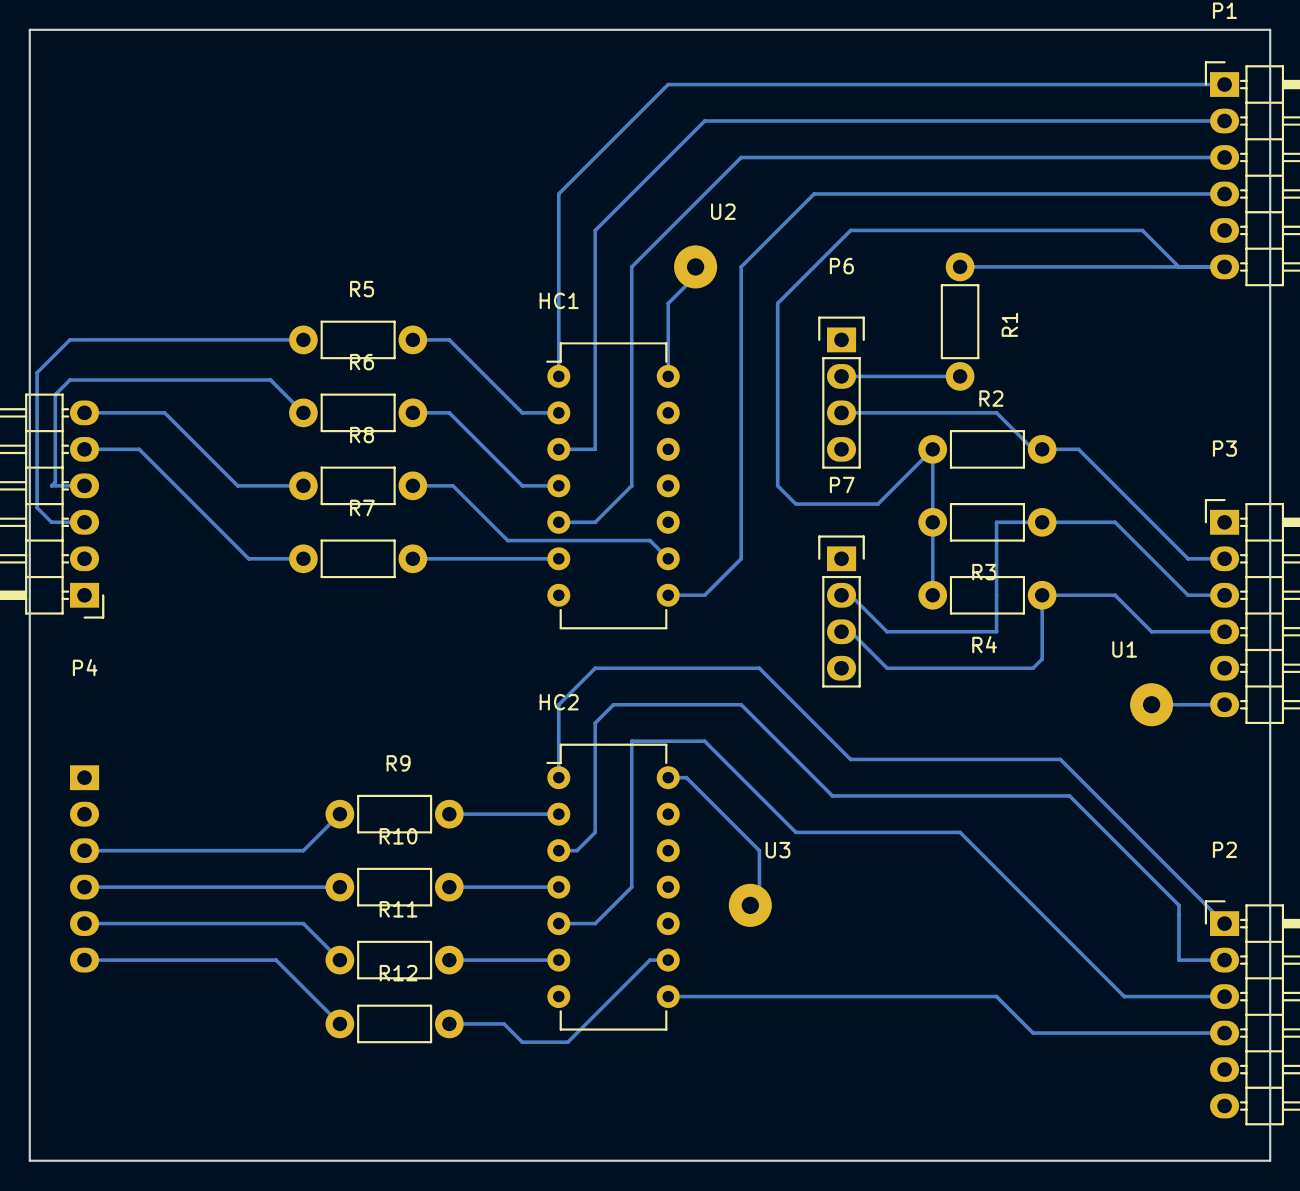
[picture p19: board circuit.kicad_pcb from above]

Board: 2 copper layers, 86.4 x 78.7 mm, 24 parts (1 on the bottom side), 32 nets.

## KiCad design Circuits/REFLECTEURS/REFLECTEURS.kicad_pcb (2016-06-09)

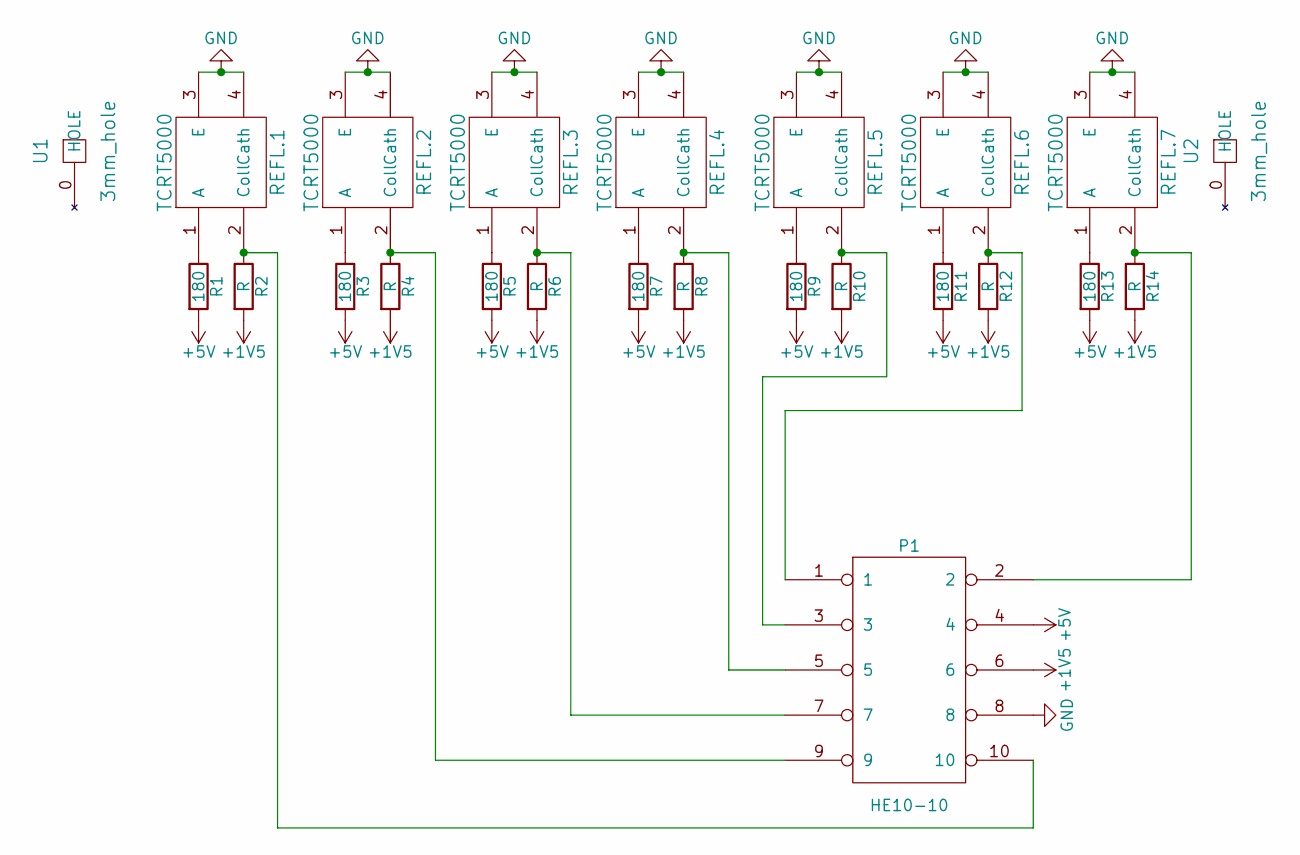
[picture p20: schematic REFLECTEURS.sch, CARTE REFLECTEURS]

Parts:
P1: HE10-10
R1, R3, R5, R7, R9, R11, R13: 180; Resistor_Horizontal_RM7mm
R2, R4, R6, R8, R10, R12, R14: R; Resistor_Horizontal_RM7mm
REFL.1, REFL.2, REFL.3, REFL.4, REFL.5, REFL.6, REFL.7: TCRT5000; TRCT5000
U1, U2: 3mm_hole; 3mmHOLE

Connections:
+1V5: P1.6, R2.2, R4.2, R6.2, R8.2, R10.2, R12.2, R14.2
+5V: P1.4, R1.2, R3.2, R5.2, R7.2, R9.2, R11.2, R13.2
GND: P1.8, REFL.1.3 (E), REFL.1.4 (Cath), REFL.2.3 (E), REFL.2.4 (Cath), REFL.3.3 (E), REFL.3.4 (Cath), REFL.4.3 (E), REFL.4.4 (Cath), REFL.5.3 (E), REFL.5.4 (Cath), REFL.6.3 (E), REFL.6.4 (Cath), REFL.7.3 (E), REFL.7.4 (Cath)
unnamed: P1.1, R12.1, REFL.6.2 (Coll)
unnamed: P1.2, R14.1, REFL.7.2 (Coll)
unnamed: P1.3, R10.1, REFL.5.2 (Coll)
unnamed: P1.5, R8.1, REFL.4.2 (Coll)
unnamed: P1.7, R6.1, REFL.3.2 (Coll)
unnamed: P1.9, R4.1, REFL.2.2 (Coll)
unnamed: P1.10, R2.1, REFL.1.2 (Coll)
unnamed: R1.1, REFL.1.1 (A)
unnamed: R3.1, REFL.2.1 (A)
unnamed: R5.1, REFL.3.1 (A)
unnamed: R7.1, REFL.4.1 (A)
unnamed: R9.1, REFL.5.1 (A)
unnamed: R11.1, REFL.6.1 (A)
unnamed: R13.1, REFL.7.1 (A)

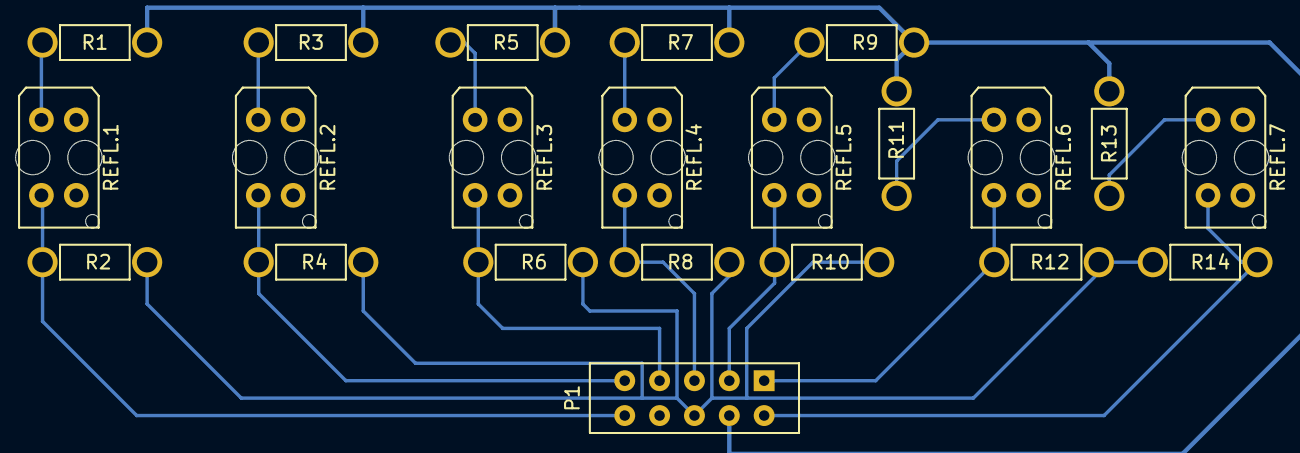
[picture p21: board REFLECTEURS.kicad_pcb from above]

Board: 2 copper layers, 24 parts (0 on the bottom side), 17 nets.

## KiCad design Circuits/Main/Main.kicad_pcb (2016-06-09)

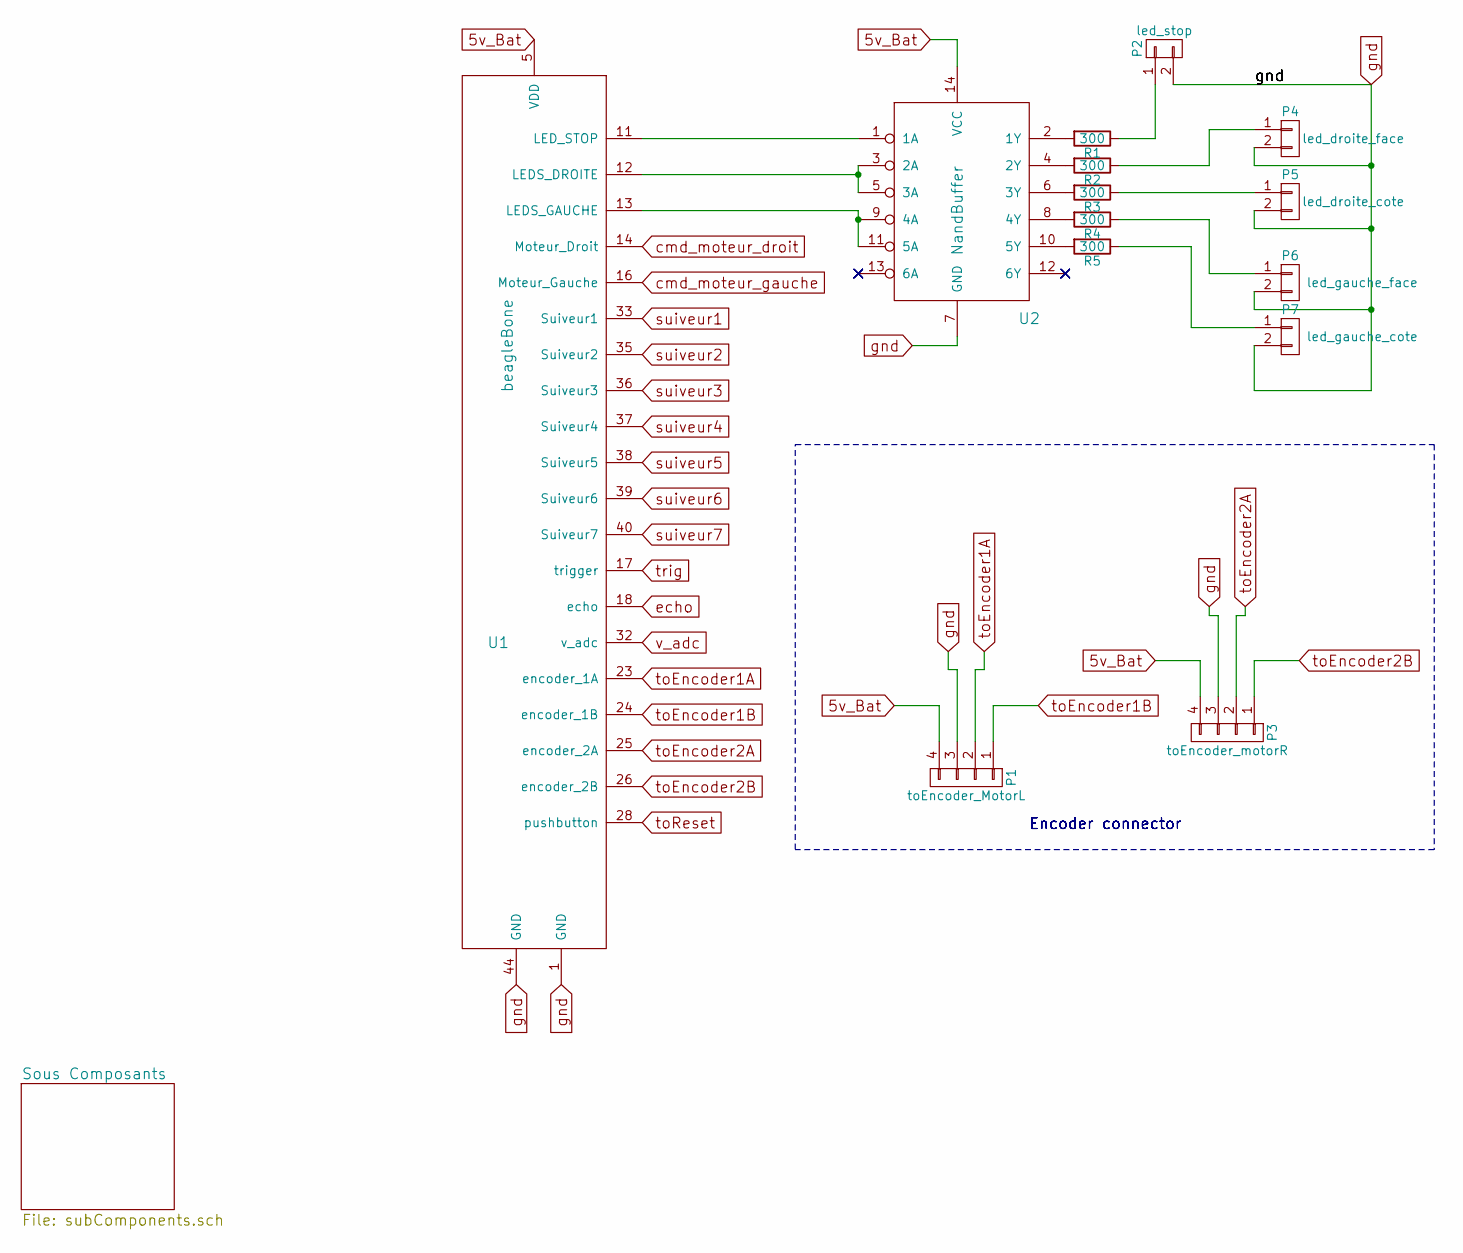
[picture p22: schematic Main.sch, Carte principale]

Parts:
P1: toEncoder_MotorL; Pin_Header_Straight_1x04
P2: led_stop; Pin_Header_Straight_1x02
P3: toEncoder_motorR; Pin_Header_Straight_1x04
P4: led_droite_face; Pin_Header_Straight_1x02
P5: led_droite_cote; Pin_Header_Straight_1x02
P6: led_gauche_face; Pin_Header_Straight_1x02
P7: led_gauche_cote; Pin_Header_Straight_1x02
R1, R2, R3, R4, R5: 300; Resistor_Horizontal_RM10mm
U1: beagleBone; beagleBoneGRNFootPrint
U2: NandBuffer

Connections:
5v_Bat: P1.4, P3.4, U1.5 (VDD), U2.14 (VCC); also elsewhere on the board
unnamed: P2.1, R1.1
unnamed: P4.1, R2.1
unnamed: P5.1, R3.1
unnamed: P6.1, R4.1
unnamed: P7.1, R5.1
unnamed: R1.2, U2.2 (1Y)
unnamed: R2.2, U2.4 (2Y)
unnamed: R3.2, U2.6 (3Y)
unnamed: R4.2, U2.8 (4Y)
unnamed: R5.2, U2.10 (5Y)
unnamed: U1.11 (LED_STOP), U2.1 (1A)
unnamed: U1.12 (LEDS_DROITE), U2.3 (2A), U2.5 (3A)
unnamed: U1.13 (LEDS_GAUCHE), U2.9 (4A), U2.11 (5A)
cmd_moteur_droit: U1.14 (Moteur_Droit); also elsewhere on the board
cmd_moteur_gauche: U1.16 (Moteur_Gauche); also elsewhere on the board
echo: U1.18 (echo); also elsewhere on the board
gnd: P1.3, P2.2, P3.3, P4.2, P5.2, P6.2, P7.2, U1.1 (GND), U1.44 (GND), U2.7 (GND); also elsewhere on the board
suiveur1: U1.33 (Suiveur1); also elsewhere on the board
suiveur2: U1.35 (Suiveur2); also elsewhere on the board
suiveur3: U1.36 (Suiveur3); also elsewhere on the board
suiveur4: U1.37 (Suiveur4); also elsewhere on the board
suiveur5: U1.38 (Suiveur5); also elsewhere on the board
suiveur6: U1.39 (Suiveur6); also elsewhere on the board
suiveur7: U1.40 (Suiveur7); also elsewhere on the board
toEncoder1A: P1.2, U1.23 (encoder_1A)
toEncoder1B: P1.1, U1.24 (encoder_1B)
toEncoder2A: P3.2, U1.25 (encoder_2A)
toEncoder2B: P3.1, U1.26 (encoder_2B)
toReset: U1.28 (pushbutton); also elsewhere on the board
trig: U1.17 (trigger); also elsewhere on the board
v_adc: U1.32 (v_adc); also elsewhere on the board

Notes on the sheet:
Encoder connector

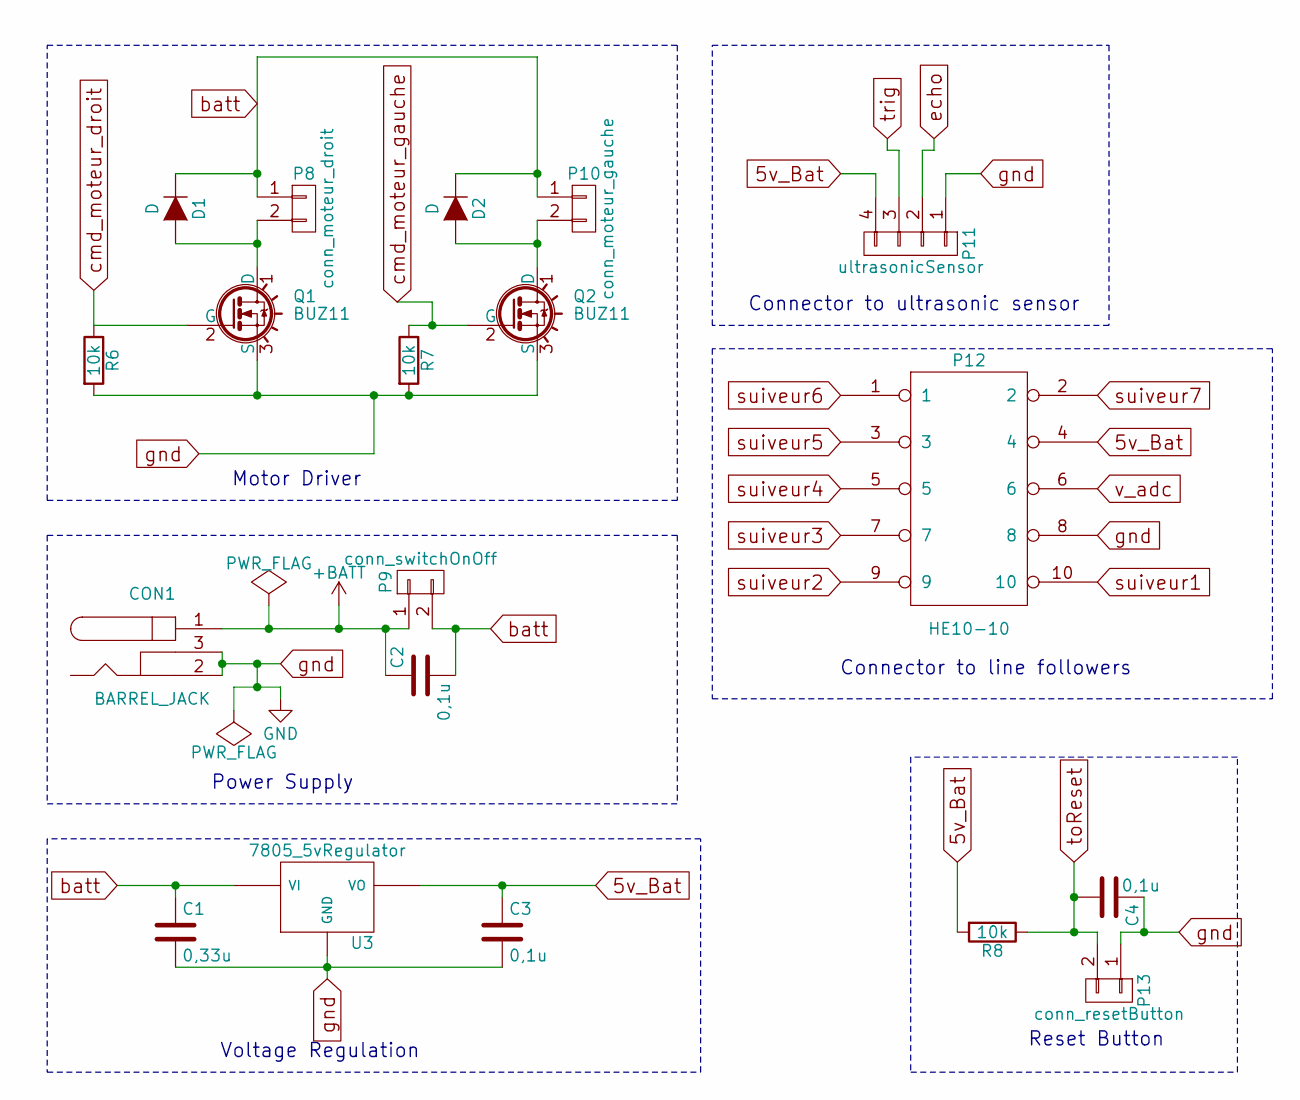
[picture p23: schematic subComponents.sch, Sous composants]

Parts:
C1: 0,33u; C_Disc_D3_P2.5
C2, C3, C4: 0,1u; C_Disc_D3_P2.5
CON1: BARREL_JACK
D1, D2: D; Diode_DO-35_SOD27_Horizontal_RM10
P8: conn_moteur_droit; Pin_Header_Straight_1x02
P9: conn_switchOnOff; Pin_Header_Straight_1x02
P10: conn_moteur_gauche; Pin_Header_Straight_1x02
P11: ultrasonicSensor; Pin_Header_Straight_1x04
P12: HE10-10; he10-10d
P13: conn_resetButton; Pin_Header_Straight_1x02
Q1, Q2: BUZ11; TO-220
R6, R7, R8: 10k; Resistor_Horizontal_RM10mm
U3: 7805_5vRegulator; voltageRegulator5v

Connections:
5v_Bat: C3.1, P11.4, P12.4, R8.2, U3.3 (VO); also elsewhere on the board
+BATT: C2.1, CON1.1, P9.1
unnamed: D1.2 (A), P8.2, Q1.1 (D)
unnamed: D2.2 (A), P10.2, Q2.1 (D)
batt: C1.1, C2.2, D1.1 (K), D2.1 (K), P8.1, P9.2, P10.1, U3.1 (VI)
cmd_moteur_droit: Q1.2 (G), R6.1; also elsewhere on the board
cmd_moteur_gauche: Q2.2 (G), R7.1; also elsewhere on the board
echo: P11.2; also elsewhere on the board
gnd: C1.2, C3.2, C4.1, CON1.2, CON1.3, P11.1, P12.8, P13.1, Q1.3 (S), Q2.3 (S), R6.2, R7.2, U3.2 (GND); also elsewhere on the board
suiveur1: P12.10; also elsewhere on the board
suiveur2: P12.9; also elsewhere on the board
suiveur3: P12.7; also elsewhere on the board
suiveur4: P12.5; also elsewhere on the board
suiveur5: P12.3; also elsewhere on the board
suiveur6: P12.1; also elsewhere on the board
suiveur7: P12.2; also elsewhere on the board
toReset: C4.2, P13.2, R8.1; also elsewhere on the board
trig: P11.3; also elsewhere on the board
v_adc: P12.6; also elsewhere on the board

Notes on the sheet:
Motor Driver
Connector to ultrasonic sensor
Power Supply
Reset Button
Connector to line followers
Voltage Regulation

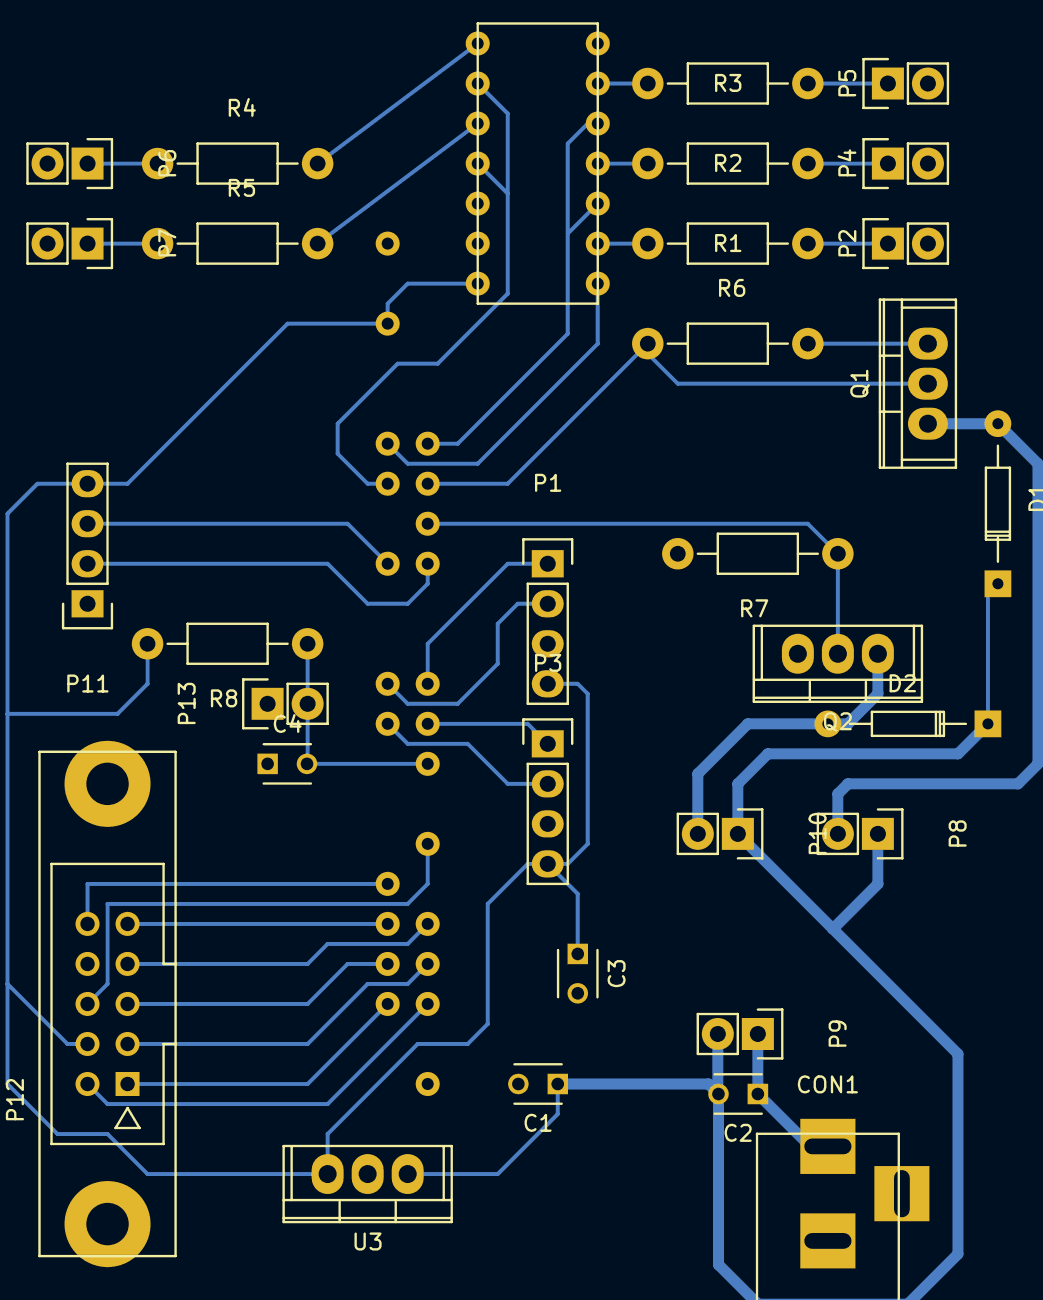
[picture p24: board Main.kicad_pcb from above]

Board: 2 copper layers, 33 parts (0 on the bottom side), 36 nets.

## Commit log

2016-03-21 Ajout de la structure du rapport
2016-03-22 Nouvelle structure de rapport
2016-04-11 Integration du plan final avec references et annexes
    [capteurs_IR.kicad_pcb, capteurs_IR.sch]
2016-04-19 MAJ du rapport
    [BeagleBone_Pinout.xlsx]
2016-05-12 Nouveau logo IPSA, nouvelles illustration et debut de solution de suivi de ligne
2016-05-16 Structure de dossiers plus clean, utilisation de projet Sublime-Text et ajout d'instructions de compilation LaTeX
2016-06-05 Tres gros changements sur l'ensemble
    [BBG.CATPart, BBG_Cap.CATPart, BBG_Product.CATProduct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]
2016-06-06 Corrections et rédaction sur la partie 3
2016-06-06 Carte mère
    [Main.kicad_pcb, Main.sch]
2016-06-07 Redimmensionnement des images matricielles
2016-06-08 MAJ biblio
    [Pour MA.xlsx]
2016-06-08 Ajout de graphics
2016-06-08 Compilation des deux versions
2016-06-09 Amelioration carte reflecteurs (simple face)
    [REFLECTEURS.kicad_pcb, REFLECTEURS.sch]
2016-06-09 Ajout de la carte principale (schemas + gerbers) et intégration
    [Main.kicad_pcb, Main.sch, components.sch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]
2016-06-09 Ameliorations cartes + rapport
    [Main.kicad_pcb, Main.sch, REFLECTEURS.kicad_pcb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]
2016-06-09 Redaction Reconnaissance d'image + MaJ Schemas/gerbers
    [Main.sch]
2016-06-09 Ajout partie couts
    [Pour MA.xlsx]
2016-06-10 Reconnaissance d'image + Abstract + Corrections diverses + Detections
    [carte Circuit.kicad_pcb, carte Circuit.sch]
2016-06-10 Ajout de la partie carte circuit
2016-06-10 Ajout de la partie moteur
